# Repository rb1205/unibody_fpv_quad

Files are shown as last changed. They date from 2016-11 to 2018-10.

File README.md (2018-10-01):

# Unibody FPV quad

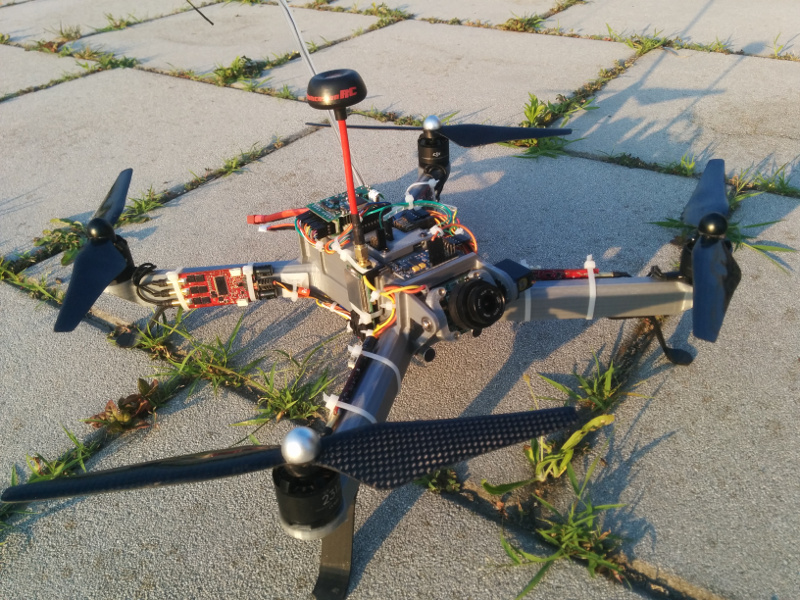
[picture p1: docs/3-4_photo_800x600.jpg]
Quad photo


A size class 400 FPV quadcopter assembled over a single piece FDM printable body, designed for long range freestyle FPV. Some highlights:

* Good FPV flight performances for its class due to high frame rigidity (comparable to frames made from single carbon fiber sheets) and relatively low inertia moment
* servo-operated tiltable FPV CCD camera mount with 180° mechanical range integrated in the unibody frame.
* Frame has dedicated fixing points for video TX, ESC, cables, antenna,...
* Fully documented: [BOM and exploded diagram](https://github.com/rb1205/unibody_fpv_quad/raw/master/docs/assembly.pdf) of the project with all components and screws located, for easy assembly. [Wiring diagram](https://github.com/rb1205/unibody_fpv_quad/raw/master/docs/wiring_diagram.pdf) is provided, too.
* Printable & easly replaceable landing gears

## Stats

* Made for 9" props
* Typical flight time is ~15-20 minutes with a 3300 mAh 4s battery. 
* Weight is 200g for the frame alone, ~700g for the assembled quad without battery and ~1000g with a 3300 mAh 4s lipo battery
* Inertia moments around CoG are around 1, 1 and 2 Kg/dm^2 (pitch,roll,yaw)
* Battery bay size=50x38x120 mm

Due to the frame size, you'll need a bigger-than-average printer with a minimum build envelope of 320x300x50mm to print the body.

CAD files are included in the project, software used is PTC Creo V.2. 

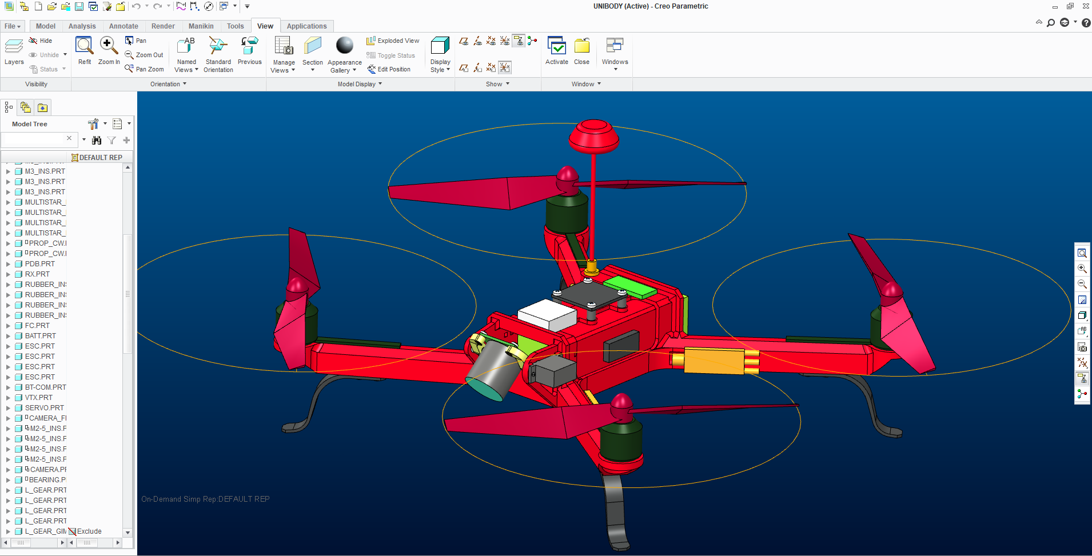
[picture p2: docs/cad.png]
Quad CAD model


Here's a [Video](https://www.youtube.com/watch?v=QMW7MYOoSNg) with a (shitty) test flight.

## Documentation

[Modal analysis](docs/modal_analysis.md)

[Print instructions](docs/print_instructions.md)

[Exploded diagram with BOM](https://github.com/rb1205/unibody_fpv_quad/raw/master/docs/assembly.pdf)

[Wiring diagram](https://github.com/rb1205/unibody_fpv_quad/raw/master/docs/wiring_diagram.pdf)

[Reference flight controller settings for iNav](config_files) (valid only for the powertrain configuration listed in the BOM)

---

This project is released under the terms of [Creative Commons Attribution-NonCommercial license](https://creativecommons.org/licenses/by-nc/4.0/)

Please contact us at riccardo.belloli@inova-soluzioni.it to discuss commercial usage of this project.

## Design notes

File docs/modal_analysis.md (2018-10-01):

# Modal analysis

To estimate the structure's resonating frequencies, an undamped modal analysis has been performed on a quick-and-dirty FEM model of the body with the added mass from the various mounted devices on the relevant places (namely motors+props, battery, top side electronics, PDB, camera subassembly) and a distributed additional body mass to reach the actual total weight. 

The body is supposed to be printed with commercial grade PLA. Material properties have been taken from [here](http://www.makeitfrom.com/material-properties/Polylactic-Acid-PLA-Polylactide/). As the quad arms are a shell filled with light support structure, as a conservative approach the model has the arms completely hollowed on the inside leaving the solid width and height from the reccomanded print settings (3x0.6mm perimeters, 9x0.2 top and bottom layers).

Following figure shows the meshed model

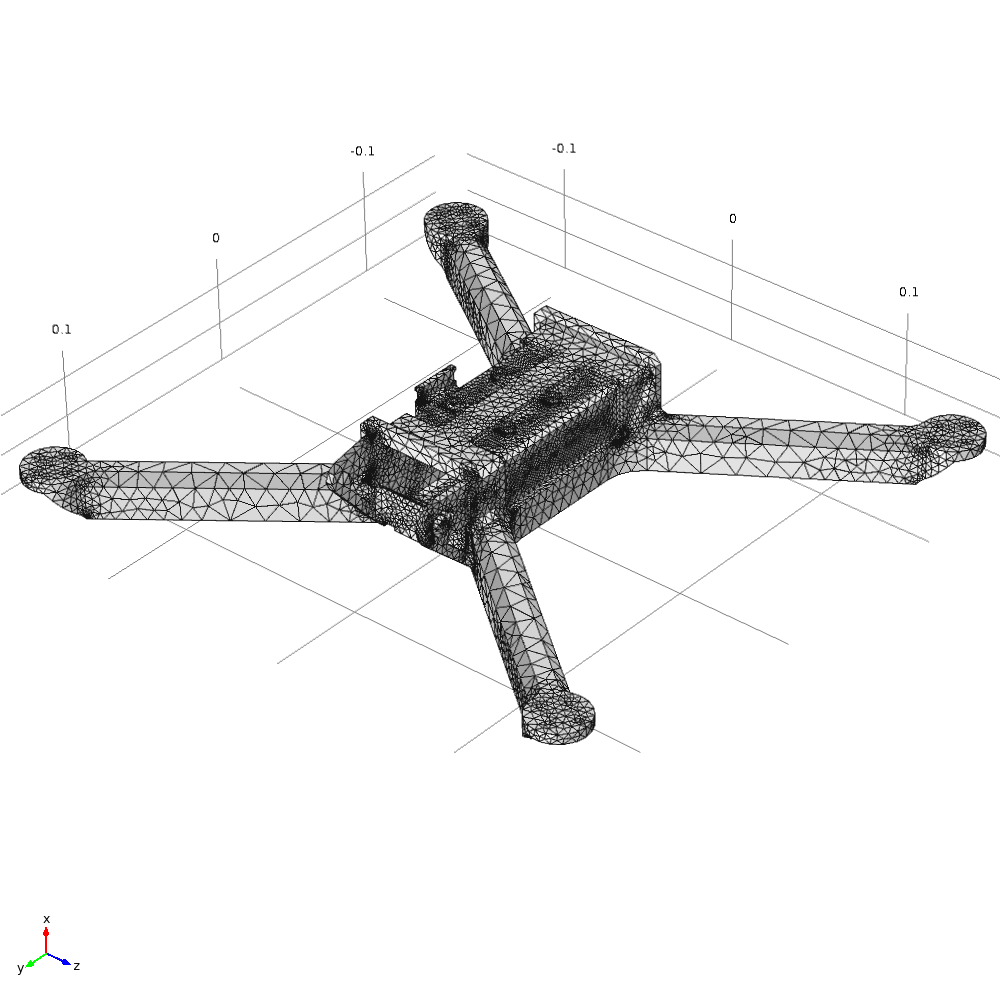
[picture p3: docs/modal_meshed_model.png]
meshed model


Analysis has been performed using Comsol Multiphysics V4.1

## Results

The following figures show the first 3 real eigenfrequencies with the relative modal shapes.

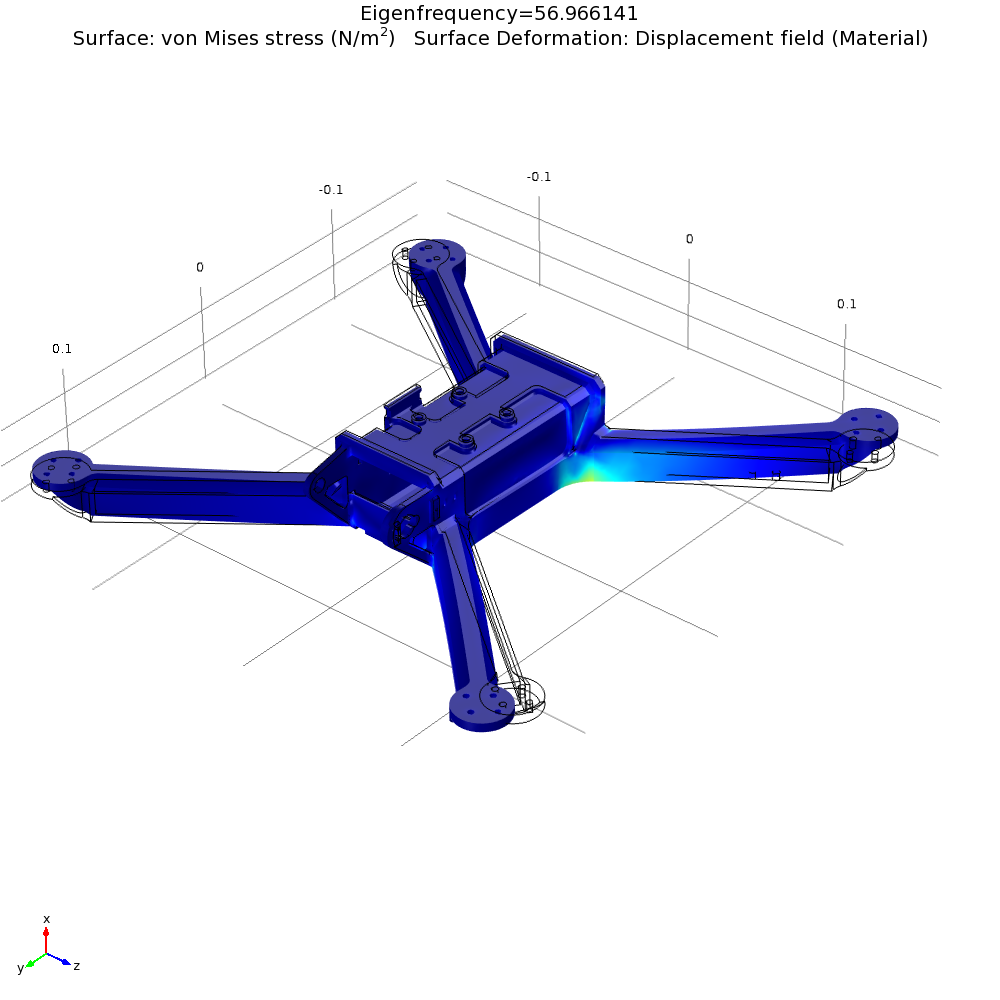
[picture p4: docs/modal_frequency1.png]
1st modal frequency

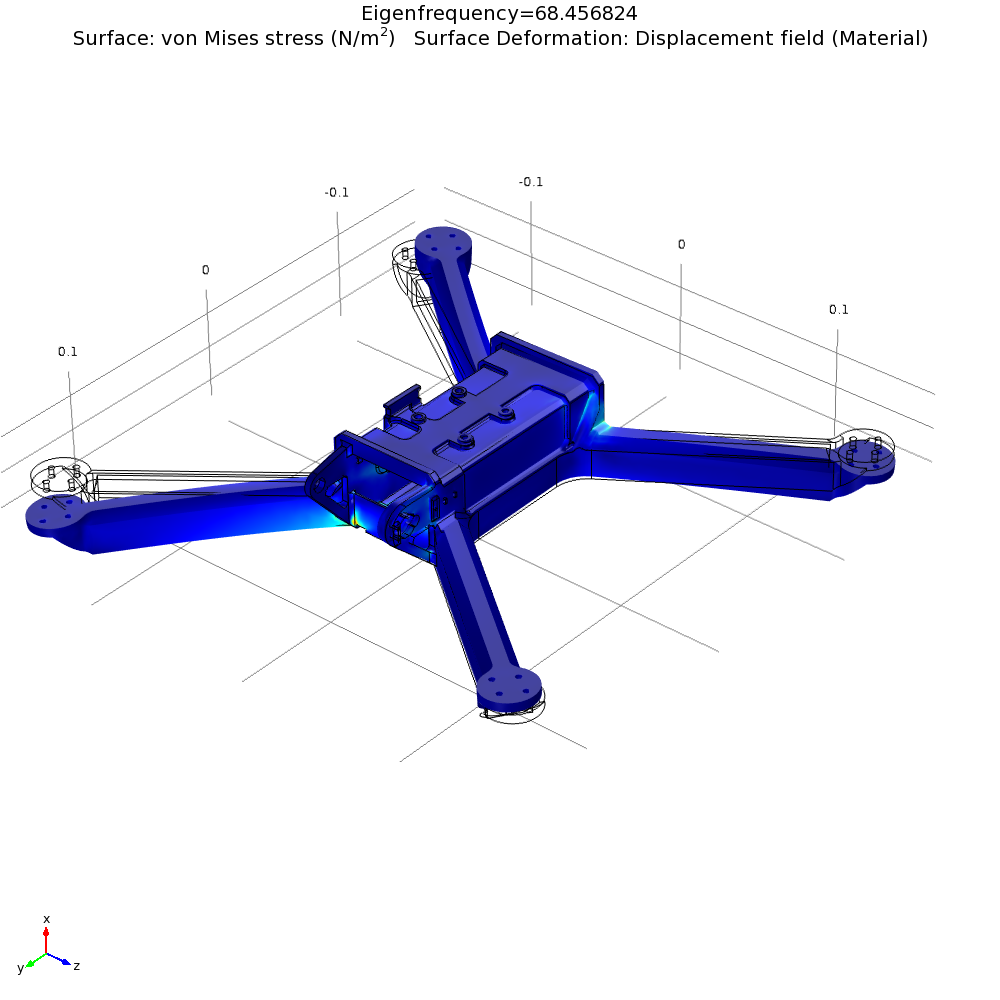
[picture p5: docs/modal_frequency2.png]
2nd modal frequency

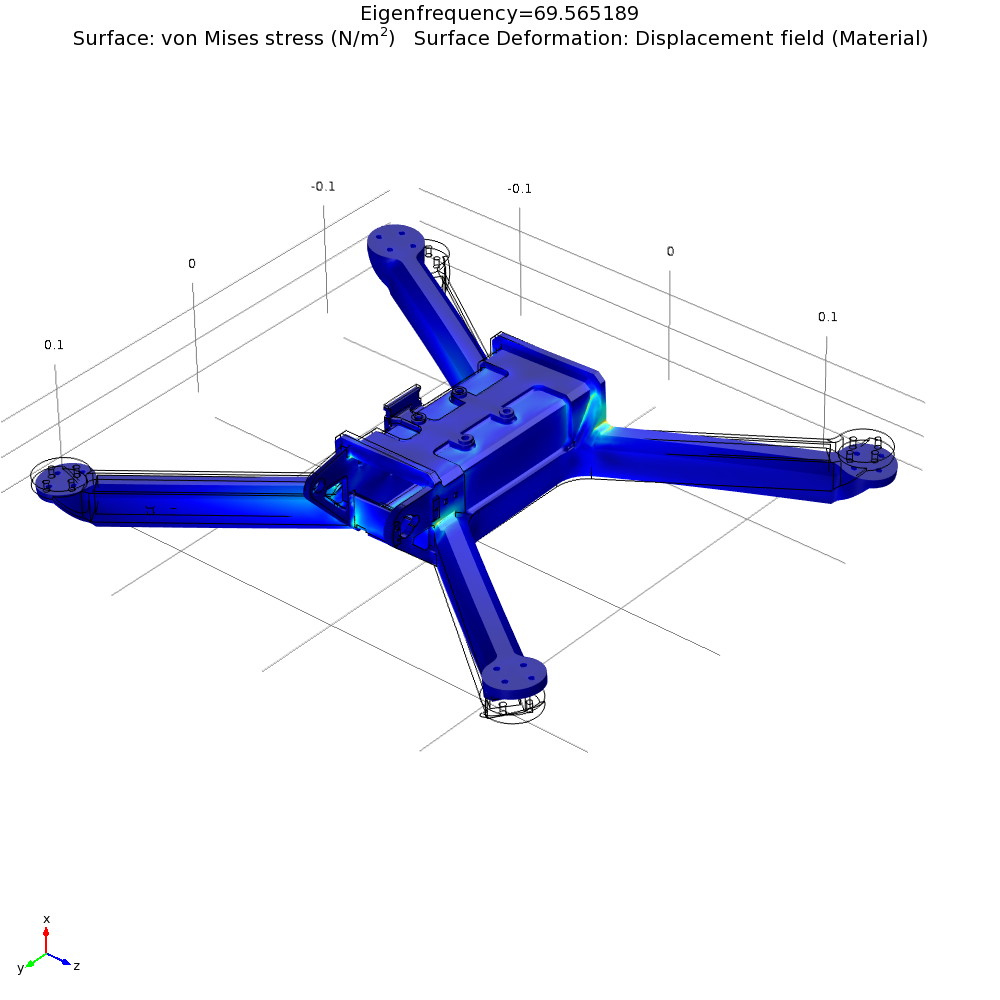
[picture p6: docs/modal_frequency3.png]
3rd modal frequency


The first free body resonation happens at about 56 Hertz and is caused by the arms vibrating on the fixing point on the central box, planarly on the horizontal plane. The second and third frequencies are similar and happen at around 68 hertz, and are due to the arms vibrating out of the horizontal plane.

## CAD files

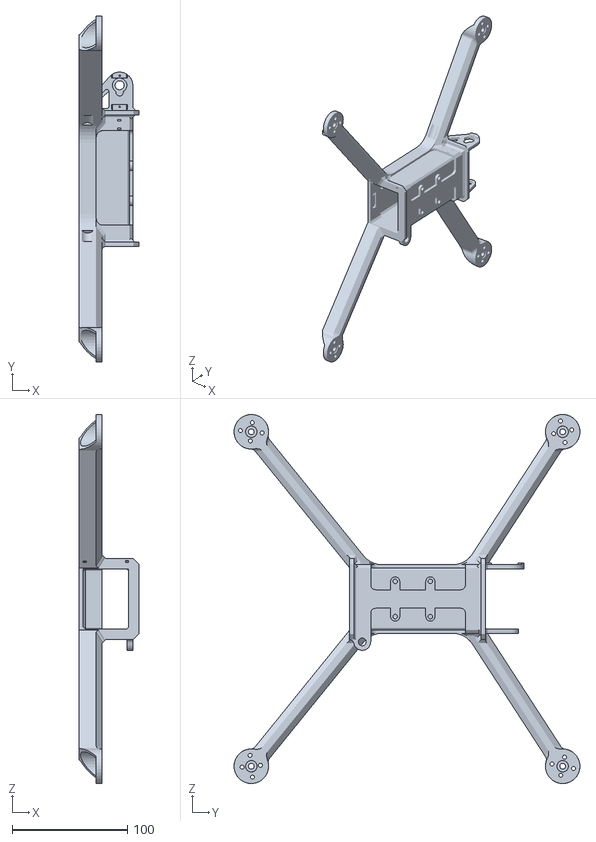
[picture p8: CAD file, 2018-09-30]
stl/body.stl
52.2 x 300.0 x 320.0

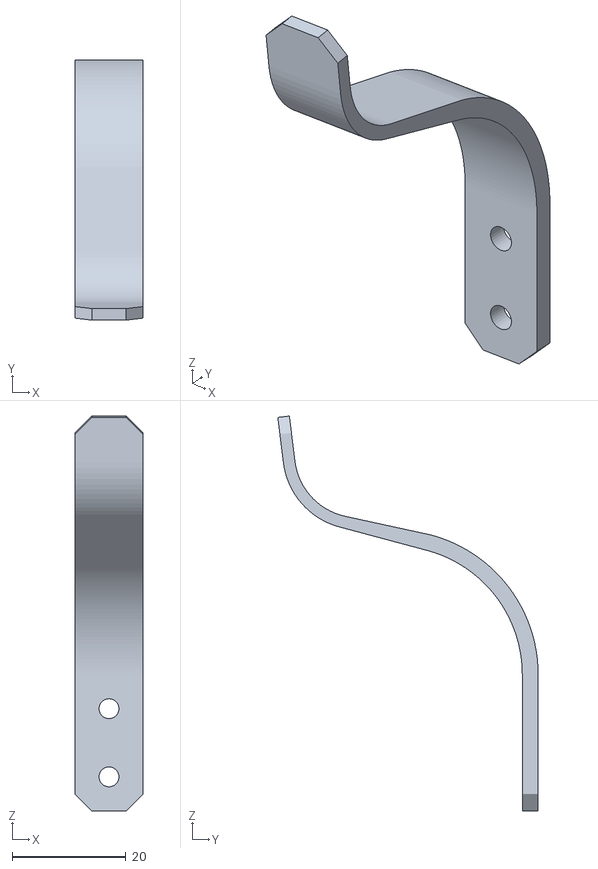
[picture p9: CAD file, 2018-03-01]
stl/l_gear.stl
12.0 x 45.8 x 69.5

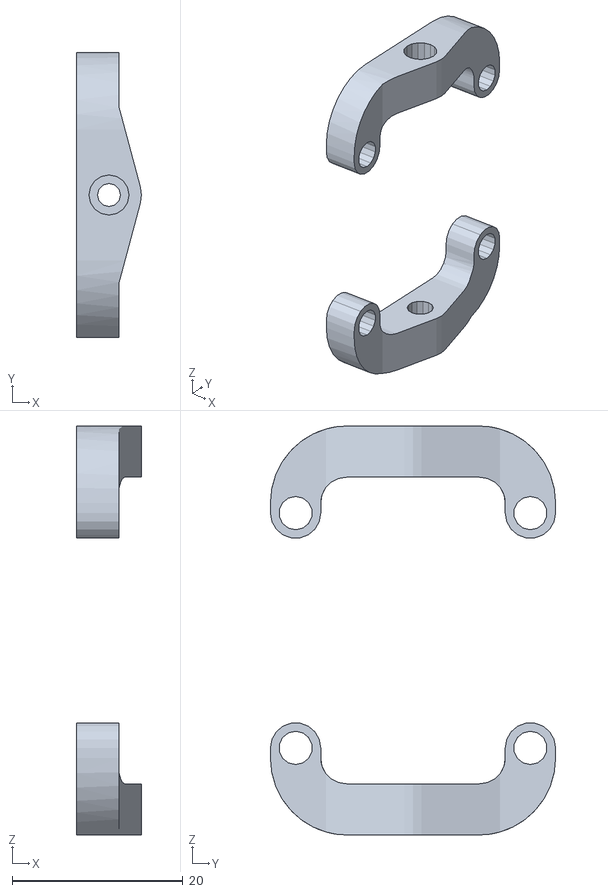
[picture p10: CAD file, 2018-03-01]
stl/camera_frame.stl
7.60 x 33.4 x 47.9

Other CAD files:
docs/wiring_diagram.dwg

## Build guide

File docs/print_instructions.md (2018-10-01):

### Body

To print this part you'll need a printer with a minimum printing envelope of 320x300x50mm.

Please observe the following print parameter carefully. The frame has been designed and verified with these settings, using different parameters may alter basilar charateristics like strength, rigidity, stress concetration points, inertia charateristics....

* Material: PLA 
* Nozzle: 0.5mm
* Extrusion width: 0.6mm
* Perimeter outlines: 3
* Layer height: 10mm
* Top solid layers: 9
* Bottom solid layers: 9
* Infill pattern: honeycomb

You are free to set all the remaining printing options as they best suit your printer.

##### Support

You'll need support structures to print the motor support pads, the cutouts near the camera mount and the top of the battery box, and expecially the latter may become hard to remove. To make it simple, set your slicer to build the support parallel to the lateral walls, so that you can extract it by pulling from the open end. The following figure shows what the preview should look like (slicer: simplify3d).
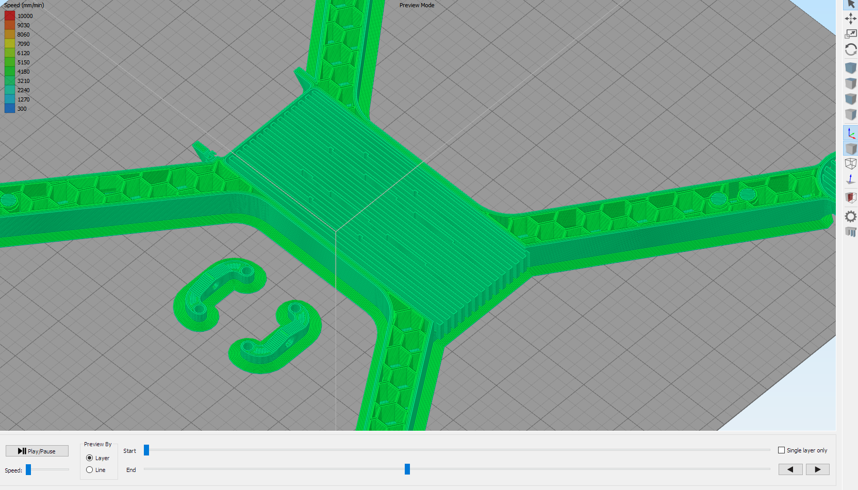
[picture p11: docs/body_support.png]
Support material example


Make sure the slicer is not placing any support in the antenna passage!

### Landing gears

Material: Carbon fiber loaded nylon or ABS

Print this part completely solid

### Camera Frame

Material: Whatever

You're free to print this part as you wish as long as the resulting part is completely solid.

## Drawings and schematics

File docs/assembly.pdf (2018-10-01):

1

A

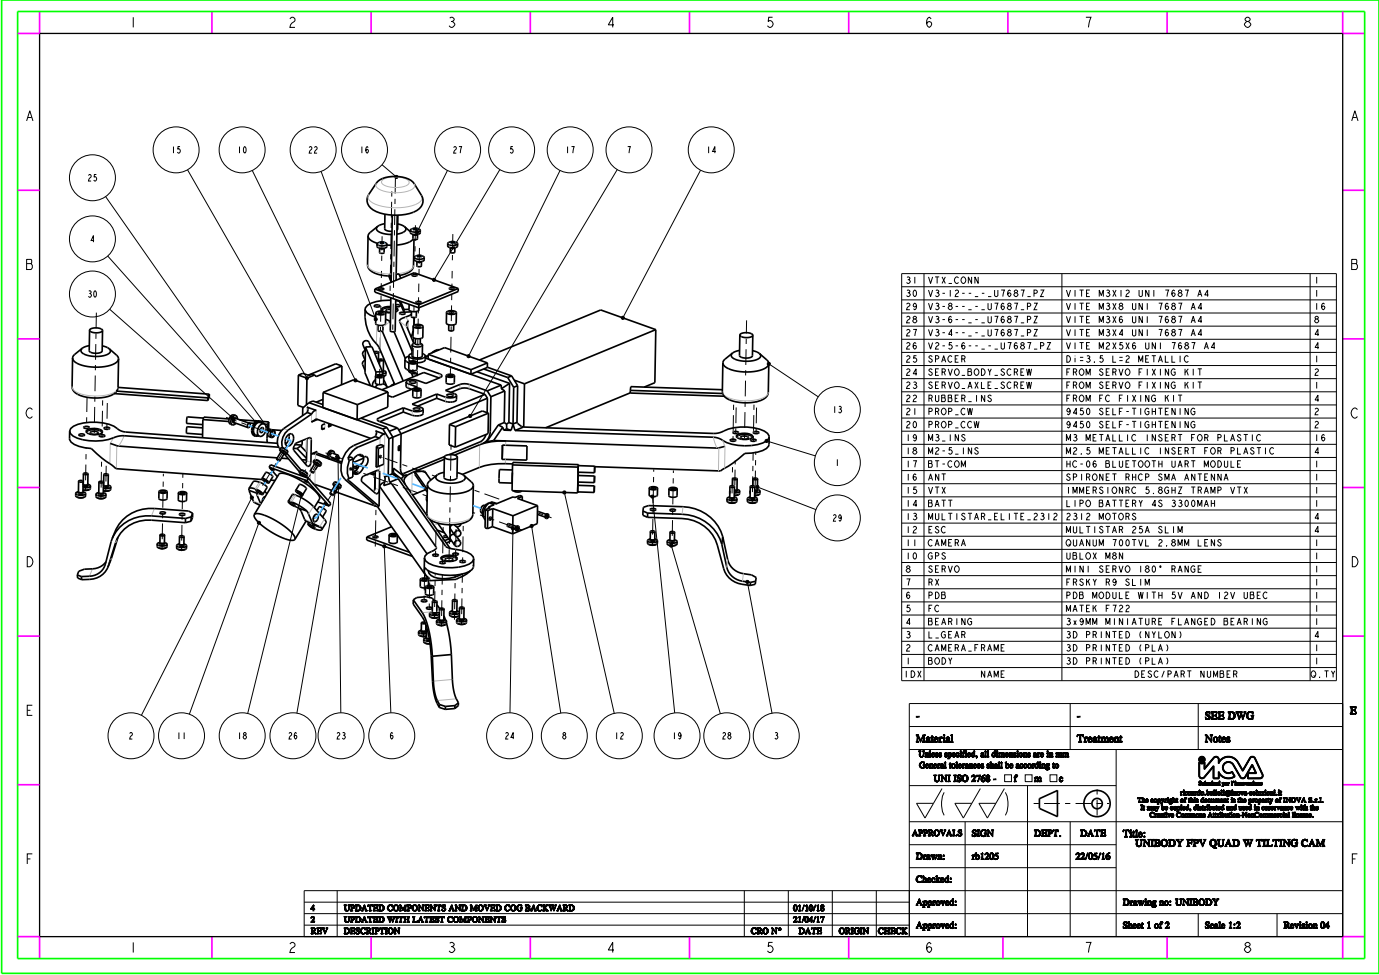
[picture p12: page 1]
SEE DWG; Material; Treatment; Notes; APPROVALS SIGN; DEPT.; DATE; Drawn:; Checked:; Approved:; Drawing no: UNIBODY; Sheet 1 of 2; Scale 1:2; Revision 04; UPDATED COMPONENTS AND MOVED COG BACKWARD; UPDATED WITH LATEST COMPONENTS; REV; DESCRIPTION; CRO N°; ORIGIN CHECK; IDX; NAME; DESC/PART NUMBER; 1 BODY; 3D PRINTED (PLA); 2 CAMERA_FRAME; 3 L_GEAR; 3D PRINTED (NYLON); 4 BEARING; 3x9MM MINIATURE FLANGED BEARING; MATEK F722; 6 PDB; PDB MODULE WITH 5V AND 12V UBEC; FRSKY R9 SLIM; 8 SERVO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

Unless specified, all dimensions are in mm
General tolerances shall be according to
UNI ISO 2768 - o-

Soluzioni per l'innovazione
riccardo.belloli@inova-soluzioni.it

The copyright of this document is the property of INOVA S.r.l.
It may be copied, distributed and used in osservance with the
Creative Commons Attribution-NonCommercial license.
Title:
UNIBODY FPV QUAD W TILTING CAM

1

A

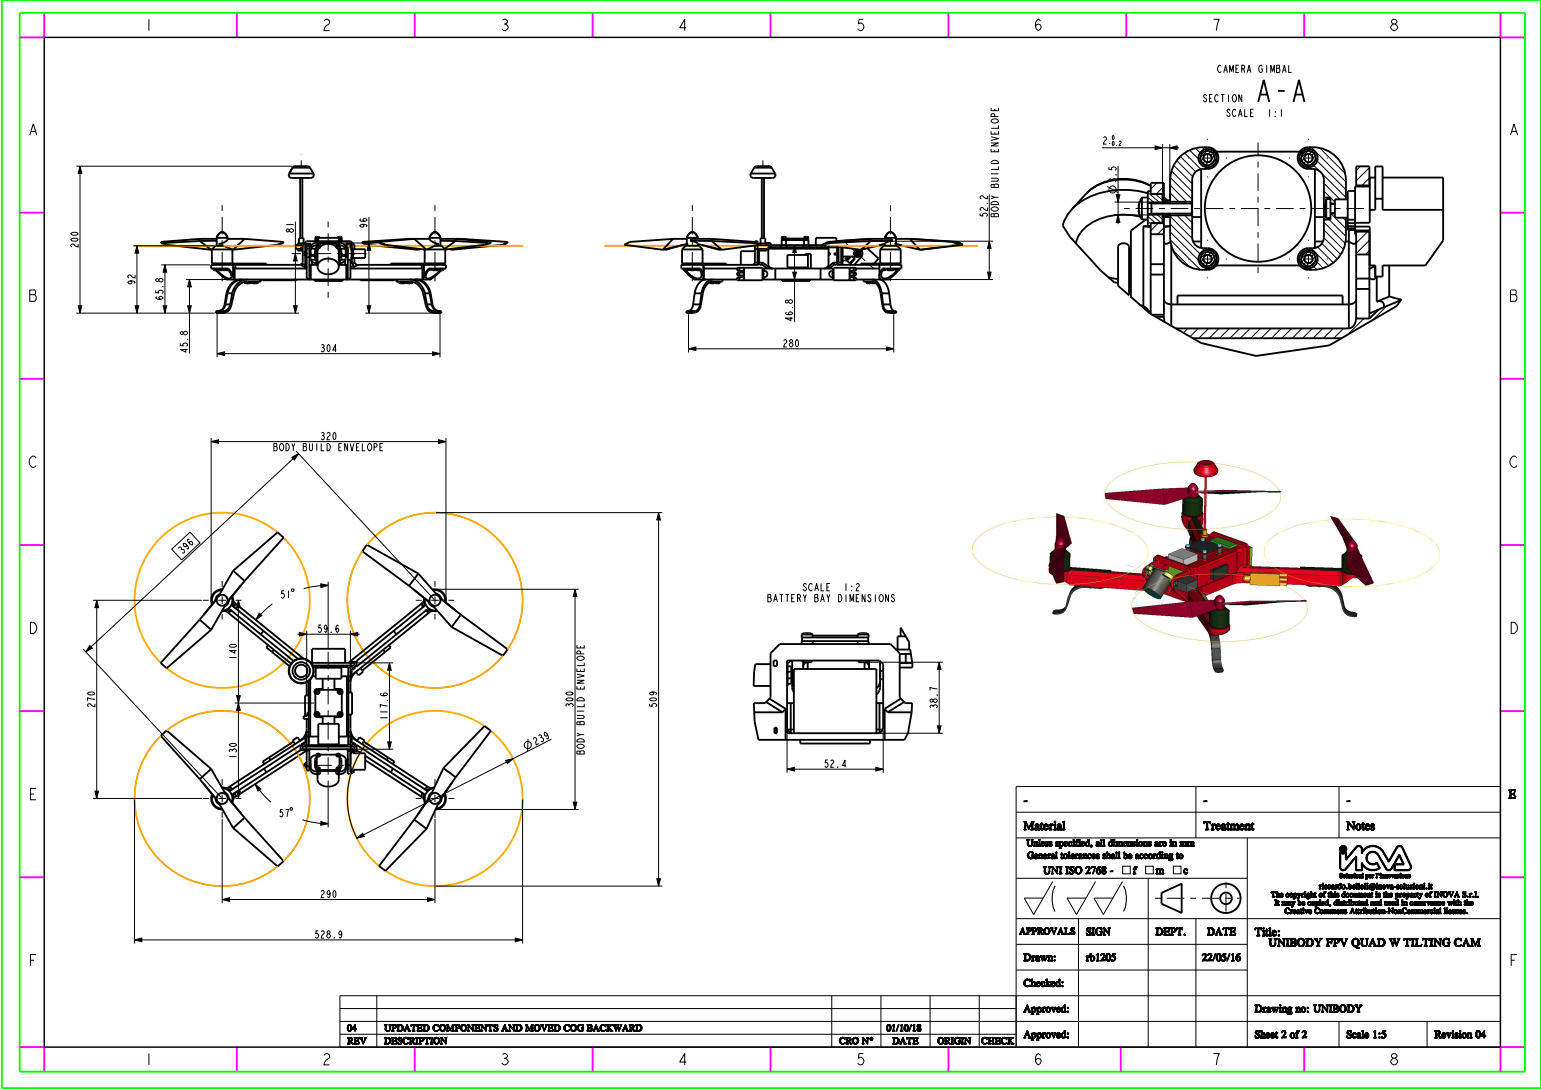
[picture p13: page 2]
Material; Treatment; Notes; APPROVALS SIGN; DEPT.; DATE; Drawn:; Checked:; Approved:; Drawing no: UNIBODY; Sheet 2 of 2; Scale 1:5; Revision 04 ⁰⁴; UPDATED COMPONENTS AND MOVED COG BACKWARD; REV; DESCRIPTION; CRO N°; ORIGIN CHECK; CAMERA GIMBAL SECTION A-A SCALE 1:1

BODY BUILD ENVELOPE

SCALE 1:2
BATTERY BAY DIMENSIONS

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

Soluzioni per l'innovazione
riccardo.belloli@inova-soluzioni.it

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

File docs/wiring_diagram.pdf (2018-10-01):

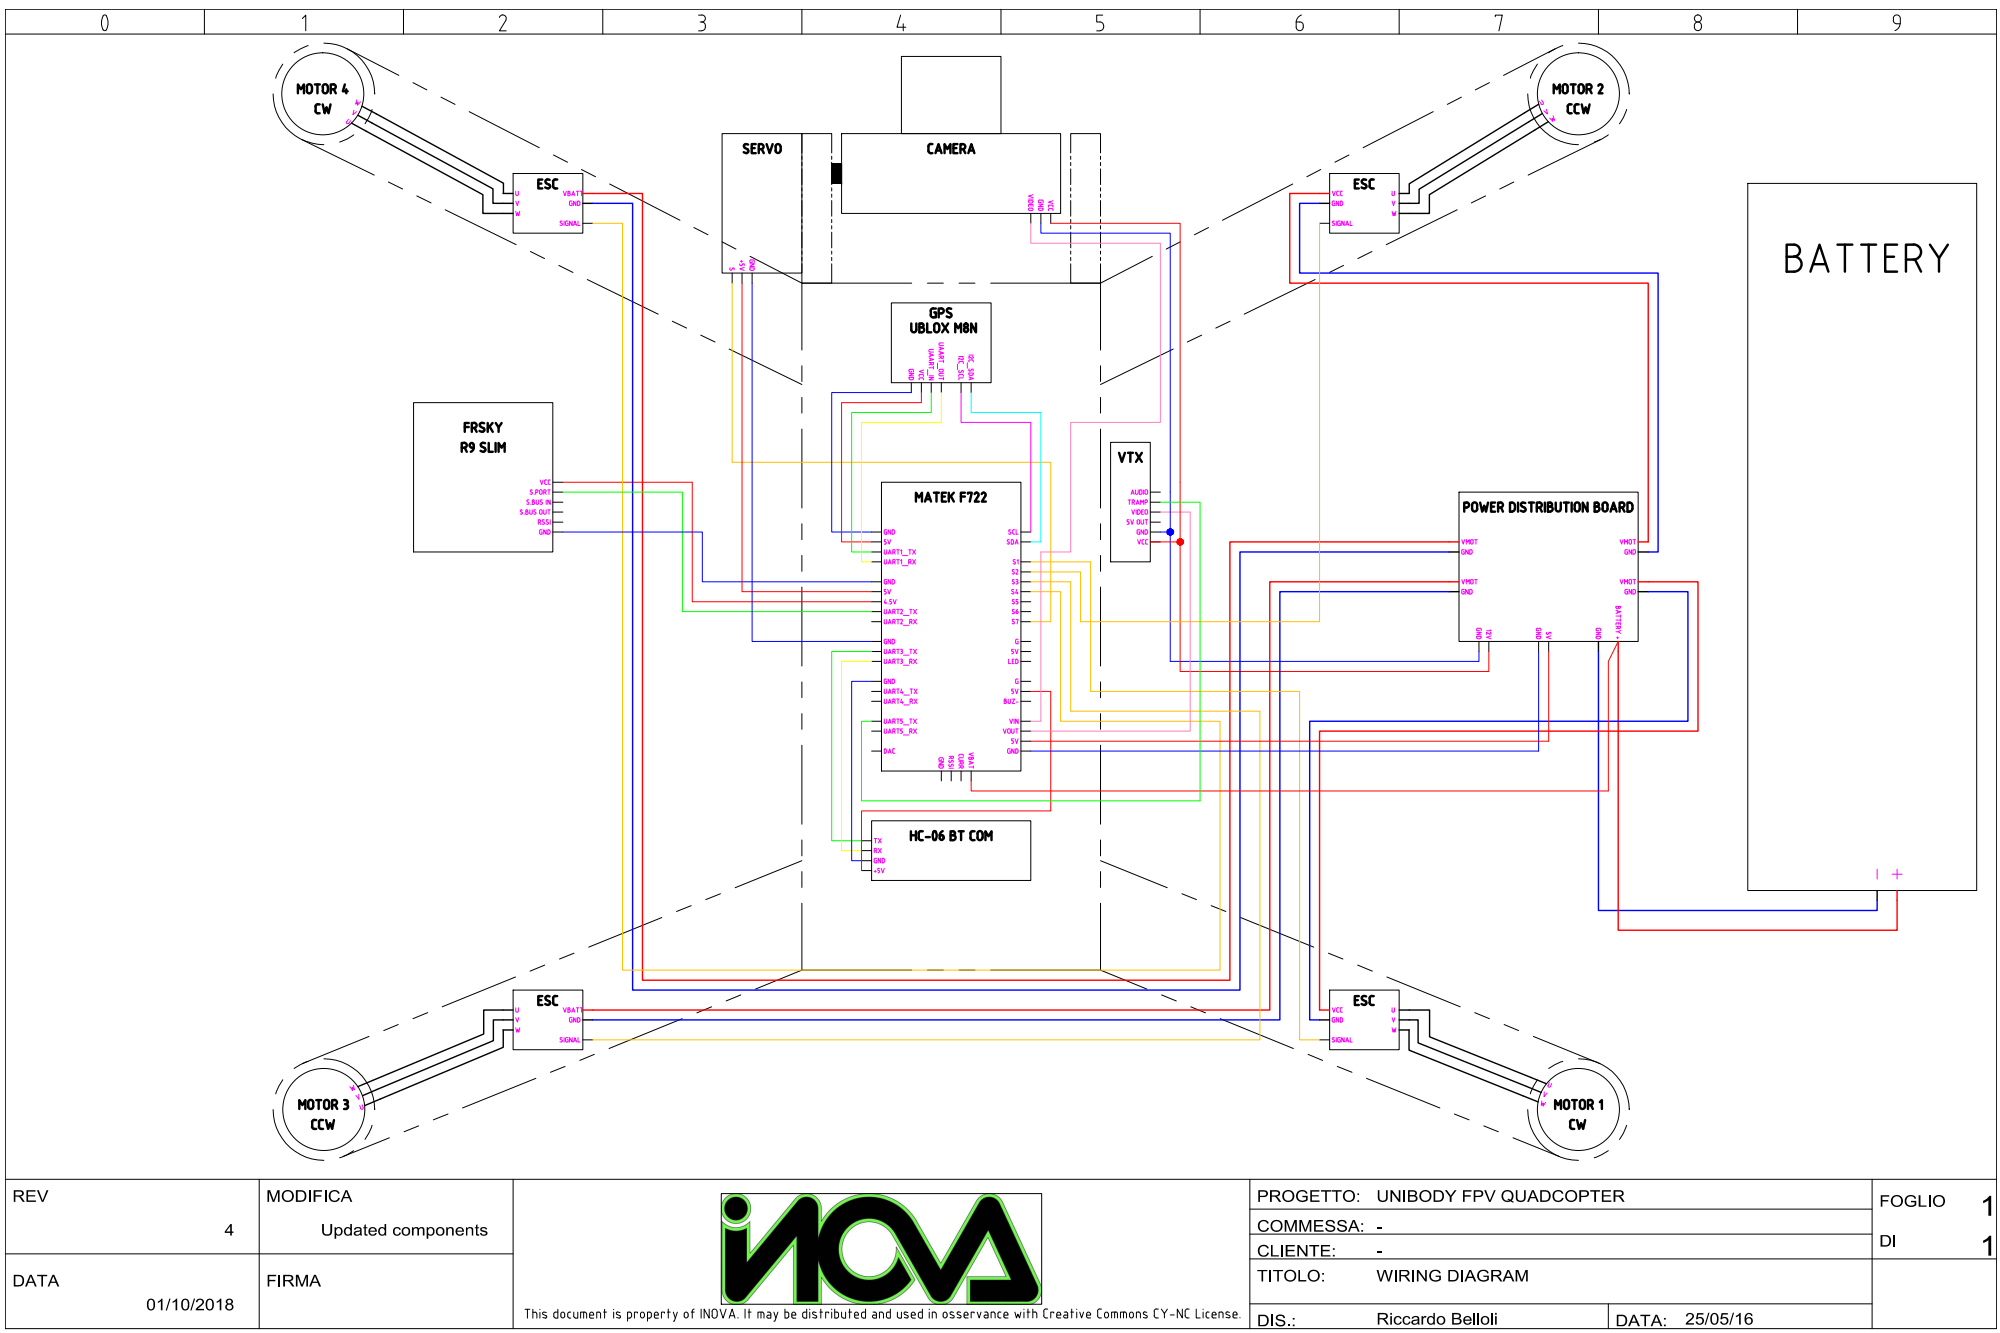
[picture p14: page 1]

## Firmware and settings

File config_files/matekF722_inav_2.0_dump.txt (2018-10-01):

# version
# INAV/MATEKF722 2.0.0 Aug 20 2018 / 19:21:31 (dbdd1656a)

# resources

# mixer

mmix reset

mmix 0  1.000 -1.000  1.000 -1.000
mmix 1  1.000 -1.000 -1.000  1.000
mmix 2  1.000  1.000  1.000  1.000
mmix 3  1.000  1.000 -1.000 -1.000

# servo mix
smix reset

smix 0 1 12 100 0
smix 1 1 9 100 0
smix 2 0 12 100 0

# servo
servo 0 1000 2000 1500 100
servo 1 700 2300 1500 100
servo 2 1000 2000 1500 100
servo 3 1000 2000 1500 100
servo 4 1000 2000 1500 100
servo 5 1000 2000 1500 100
servo 6 1000 2000 1500 100
servo 7 1000 2000 1500 100

# feature
feature -THR_VBAT_COMP
feature -VBAT
feature -TX_PROF_SEL
feature -BAT_PROF_AUTOSWITCH
feature -MOTOR_STOP
feature -SOFTSERIAL
feature -GPS
feature -TELEMETRY
feature -CURRENT_METER
feature -3D
feature -RX_PARALLEL_PWM
feature -RX_MSP
feature -RSSI_ADC
feature -LED_STRIP
feature -DASHBOARD
feature -BLACKBOX
feature -TRANSPONDER
feature -AIRMODE
feature -SUPEREXPO
feature -VTX
feature -RX_SPI
feature -PWM_SERVO_DRIVER
feature -PWM_OUTPUT_ENABLE
feature -OSD
feature -FW_LAUNCH
feature -TRACE
feature VBAT
feature TELEMETRY
feature CURRENT_METER
feature LED_STRIP
feature BLACKBOX
feature PWM_OUTPUT_ENABLE
feature OSD

# beeper
beeper RUNTIME_CALIBRATION
beeper HW_FAILURE
beeper RX_LOST
beeper RX_LOST_LANDING
beeper DISARMING
beeper ARMING
beeper ARMING_GPS_FIX
beeper BAT_CRIT_LOW
beeper BAT_LOW
beeper GPS_STATUS
beeper RX_SET
beeper ACTION_SUCCESS
beeper ACTION_FAIL
beeper READY_BEEP
beeper MULTI_BEEPS
beeper DISARM_REPEAT
beeper ARMED
beeper SYSTEM_INIT
beeper ON_USB
beeper LAUNCH_MODE
beeper CAM_CONNECTION_OPEN
beeper CAM_CONNECTION_CLOSED

# map
map AETR

# serial
serial 20 1 115200 38400 0 115200
serial 0 0 115200 38400 0 115200
serial 1 64 115200 38400 0 115200
serial 2 2 115200 38400 0 115200
serial 3 0 115200 38400 0 115200
serial 4 4096 115200 38400 0 115200

# led
led 0 0,0::AOW:10
led 1 1,0::AOW:1
led 2 2,0::AOW:1
led 3 3,0::AOW:1
led 4 4,0::AOW:1
led 5 5,0::AOW:10
led 6 0,0::C:0
led 7 0,0::C:0
led 8 0,0::C:0
led 9 0,0::C:0
led 10 0,0::C:0
led 11 0,0::C:0
led 12 0,0::C:0
led 13 0,0::C:0
led 14 0,0::C:0
led 15 0,0::C:0
led 16 0,0::C:0
led 17 0,0::C:0
led 18 0,0::C:0
led 19 0,0::C:0
led 20 0,0::C:0
led 21 0,0::C:0
led 22 0,0::C:0
led 23 0,0::C:0
led 24 0,0::C:0
led 25 0,0::C:0
led 26 0,0::C:0
led 27 0,0::C:0
led 28 0,0::C:0
led 29 0,0::C:0
led 30 0,0::C:0
led 31 0,0::C:0

# color
color 0 0,0,0
color 1 0,255,255
color 2 0,0,255
color 3 30,0,255
color 4 60,0,255
color 5 90,0,255
color 6 120,0,255
color 7 150,0,255
color 8 180,0,255
color 9 210,0,255
color 10 240,0,255
color 11 270,0,255
color 12 300,0,255
color 13 330,0,255
color 14 0,0,0
color 15 0,0,0

# mode_color
mode_color 0 0 1
mode_color 0 1 11
mode_color 0 2 2
mode_color 0 3 13
mode_color 0 4 10
mode_color 0 5 3
mode_color 1 0 5
mode_color 1 1 11
mode_color 1 2 3
mode_color 1 3 13
mode_color 1 4 10
mode_color 1 5 3
mode_color 2 0 10
mode_color 2 1 11
mode_color 2 2 4
mode_color 2 3 13
mode_color 2 4 10
mode_color 2 5 3
mode_color 3 0 8
mode_color 3 1 11
mode_color 3 2 4
mode_color 3 3 13
mode_color 3 4 10
mode_color 3 5 3
mode_color 4 0 7
mode_color 4 1 11
mode_color 4 2 3
mode_color 4 3 13
mode_color 4 4 10
mode_color 4 5 3
mode_color 5 0 9
mode_color 5 1 11
mode_color 5 2 2
mode_color 5 3 13
mode_color 5 4 10
mode_color 5 5 3
mode_color 6 0 2
mode_color 6 1 6
mode_color 6 2 1
mode_color 6 3 0
mode_color 6 4 0
mode_color 6 5 2
mode_color 6 6 3
mode_color 6 7 6
mode_color 6 8 0
mode_color 6 9 0
mode_color 6 10 0

# aux
aux 0 0 0 1350 2100
aux 1 1 2 1800 2100
aux 2 2 2 1350 1650
aux 3 20 0 1800 2100
aux 4 4 5 1350 1650
aux 5 5 5 1800 2100
aux 6 6 8 900 1200
aux 7 7 10 1400 1600
aux 8 3 4 1350 2100
aux 9 9 3 1050 2100
aux 10 8 3 1800 2100
aux 11 19 3 1350 1650
aux 12 21 8 1800 2100
aux 13 11 10 1800 2100
aux 14 15 6 1800 2100
aux 15 18 7 1800 2100
aux 16 32 6 1800 2100
aux 17 0 0 900 900
aux 18 0 0 900 900
aux 19 0 0 900 900

# adjrange
adjrange 0 0 0 900 900 0 0
adjrange 1 0 0 900 900 0 0
adjrange 2 0 0 900 900 0 0
adjrange 3 0 0 900 900 0 0
adjrange 4 0 0 900 900 0 0
adjrange 5 0 0 900 900 0 0
adjrange 6 0 0 900 900 0 0
adjrange 7 0 0 900 900 0 0
adjrange 8 0 0 900 900 0 0
adjrange 9 0 0 900 900 0 0
adjrange 10 0 0 900 900 0 0
adjrange 11 0 0 900 900 0 0

# rxrange
rxrange 0 1000 2000
rxrange 1 1000 2000
rxrange 2 1000 2000
rxrange 3 1000 2000

# osd_layout
osd_layout 0 0 25 12 V
osd_layout 0 1 12 0 H
osd_layout 0 2 0 0 H
osd_layout 0 3 8 6 V
osd_layout 0 4 8 6 V
osd_layout 0 5 23 8 H
osd_layout 0 6 23 9 H
osd_layout 0 7 12 13 V
osd_layout 0 8 20 2 H
osd_layout 0 9 1 2 H
osd_layout 0 10 1 1 H
osd_layout 0 11 1 13 V
osd_layout 0 12 1 12 V
osd_layout 0 13 1 7 V
osd_layout 0 14 25 13 V
osd_layout 0 15 24 7 V
osd_layout 0 16 2 10 H
osd_layout 0 17 2 11 H
osd_layout 0 18 2 12 H
osd_layout 0 19 15 1 H
osd_layout 0 20 18 12 H
osd_layout 0 21 0 12 H
osd_layout 0 22 14 3 V
osd_layout 0 23 2 1 V
osd_layout 0 24 12 2 H
osd_layout 0 25 22 5 H
osd_layout 0 26 24 7 H
osd_layout 0 27 3 5 H
osd_layout 0 28 22 1 V
osd_layout 0 29 23 12 H
osd_layout 0 30 1 14 V
osd_layout 0 31 0 10 H
osd_layout 0 32 12 0 V
osd_layout 0 33 6 2 H
osd_layout 0 34 10 2 V
osd_layout 0 35 1 5 H
osd_layout 0 36 1 5 H
osd_layout 0 37 1 6 H
osd_layout 0 38 24 2 H
osd_layout 0 39 1 5 H
osd_layout 0 40 1 2 H
osd_layout 0 41 1 8 H
osd_layout 0 42 1 7 H
osd_layout 0 43 0 0 H
osd_layout 0 44 0 0 H
osd_layout 0 45 0 0 H
osd_layout 0 46 3 6 H
osd_layout 0 47 3 7 H
osd_layout 0 48 23 7 H
osd_layout 0 49 23 6 H
osd_layout 0 50 0 0 H
osd_layout 0 51 12 2 H
osd_layout 0 52 12 2 H
osd_layout 0 53 12 1 H
osd_layout 0 54 12 1 V
osd_layout 0 55 18 0 V
osd_layout 0 56 2 12 H
osd_layout 0 57 2 12 H
osd_layout 0 58 2 12 H
osd_layout 0 59 2 12 H
osd_layout 0 60 2 12 H
osd_layout 0 61 2 12 H
osd_layout 0 62 2 10 H
osd_layout 0 63 2 11 H
osd_layout 0 64 2 12 H
osd_layout 0 65 2 12 H
osd_layout 0 66 2 12 H
osd_layout 0 67 2 12 H
osd_layout 0 68 2 12 H
osd_layout 0 69 2 12 H
osd_layout 0 70 2 12 H
osd_layout 0 71 2 12 H
osd_layout 0 72 2 12 H
osd_layout 0 73 2 12 H
osd_layout 0 74 2 12 H
osd_layout 0 75 2 12 H
osd_layout 0 76 2 12 H
osd_layout 0 77 2 12 H
osd_layout 0 78 0 0 H
osd_layout 0 79 2 12 H
osd_layout 0 80 2 12 H
osd_layout 0 81 2 12 H
osd_layout 0 82 2 12 H
osd_layout 0 83 2 12 H
osd_layout 0 84 2 12 H
osd_layout 1 0 23 0 V
osd_layout 1 1 12 0 H
osd_layout 1 2 0 0 H
osd_layout 1 3 8 6 H
osd_layout 1 4 8 6 H
osd_layout 1 5 23 8 H
osd_layout 1 6 23 9 H
osd_layout 1 7 12 12 H
osd_layout 1 8 20 2 H
osd_layout 1 9 1 2 H
osd_layout 1 10 1 1 V
osd_layout 1 11 1 3 H
osd_layout 1 12 1 4 H
osd_layout 1 13 23 1 H
osd_layout 1 14 25 13 V
osd_layout 1 15 1 0 H
osd_layout 1 16 2 10 H
osd_layout 1 17 2 11 H
osd_layout 1 18 2 12 H
osd_layout 1 19 15 1 H
osd_layout 1 20 9 14 V
osd_layout 1 21 9 13 V
osd_layout 1 22 14 11 H
osd_layout 1 23 1 13 V
osd_layout 1 24 12 2 H
osd_layout 1 25 23 5 H
osd_layout 1 26 24 7 H
osd_layout 1 27 3 5 H
osd_layout 1 28 23 11 H
osd_layout 1 29 23 14 V
osd_layout 1 30 1 13 H
osd_layout 1 31 25 12 V
osd_layout 1 32 12 1 H
osd_layout 1 33 6 2 H
osd_layout 1 34 18 2 H
osd_layout 1 35 1 5 H
osd_layout 1 36 1 5 H
osd_layout 1 37 1 6 H
osd_layout 1 38 1 7 H
osd_layout 1 39 1 5 H
osd_layout 1 40 1 2 H
osd_layout 1 41 1 8 H
osd_layout 1 42 1 7 H
osd_layout 1 43 0 0 V
osd_layout 1 44 0 0 H
osd_layout 1 45 0 0 H
osd_layout 1 46 1 12 H
osd_layout 1 47 1 12 H
osd_layout 1 48 23 7 H
osd_layout 1 49 23 6 H
osd_layout 1 50 0 0 H
osd_layout 1 51 1 12 H
osd_layout 1 52 1 13 H
osd_layout 1 53 12 1 H
osd_layout 1 54 12 1 H
osd_layout 1 55 1 8 H
osd_layout 1 56 2 12 H
osd_layout 1 57 2 12 H
osd_layout 1 58 2 12 H
osd_layout 1 59 2 12 H
osd_layout 1 60 2 12 H
osd_layout 1 61 2 12 H
osd_layout 1 62 2 10 H
osd_layout 1 63 2 11 H
osd_layout 1 64 2 12 H
osd_layout 1 65 2 12 H
osd_layout 1 66 2 12 H
osd_layout 1 67 2 12 H
osd_layout 1 68 2 12 H
osd_layout 1 69 2 12 H
osd_layout 1 70 2 12 H
osd_layout 1 71 2 12 H
osd_layout 1 72 2 12 H
osd_layout 1 73 2 12 H
osd_layout 1 74 2 12 H
osd_layout 1 75 2 12 H
osd_layout 1 76 2 12 H
osd_layout 1 77 2 12 H
osd_layout 1 78 0 0 H
osd_layout 1 79 2 12 H
osd_layout 1 80 2 12 H
osd_layout 1 81 2 12 H
osd_layout 1 82 2 12 H
osd_layout 1 83 2 12 H
osd_layout 1 84 2 12 H
osd_layout 2 0 23 0 H
osd_layout 2 1 12 0 H
osd_layout 2 2 0 0 H
osd_layout 2 3 8 6 H
osd_layout 2 4 8 6 H
osd_layout 2 5 23 8 H
osd_layout 2 6 23 9 H
osd_layout 2 7 12 12 H
osd_layout 2 8 20 2 H
osd_layout 2 9 1 2 H
osd_layout 2 10 8 6 H
osd_layout 2 11 1 3 H
osd_layout 2 12 1 4 H
osd_layout 2 13 23 1 H
osd_layout 2 14 0 11 H
osd_layout 2 15 1 0 H
osd_layout 2 16 2 10 H
osd_layout 2 17 2 11 H
osd_layout 2 18 2 12 H
osd_layout 2 19 15 1 H
osd_layout 2 20 18 12 H
osd_layout 2 21 0 12 H
osd_layout 2 22 14 11 H
osd_layout 2 23 1 1 H
osd_layout 2 24 12 2 H
osd_layout 2 25 23 5 H
osd_layout 2 26 24 7 H
osd_layout 2 27 3 5 H
osd_layout 2 28 23 11 H
osd_layout 2 29 23 12 H
osd_layout 2 30 1 13 H
osd_layout 2 31 0 10 H
osd_layout 2 32 12 1 H
osd_layout 2 33 6 2 H
osd_layout 2 34 18 2 H
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

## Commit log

2016-11-07 First version (no FPV)
    [body.stl, piedino.stl]
2016-11-07 Second version
    [body.stl, carrello.stl, naze32acro_top_telemetry.stl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]
2016-11-07 Cleanup for mk3
    [body.stl, carrello.stl, naze32acro_top_telemetry.stl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]
2016-11-07 added note about threaded inserts
2016-11-07 moved stl's from cad to dedicated directory
    [body.stl, camera_frame.stl, l_gear.stl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]
2016-11-07 added wiring diagram
    [wiring_diagram.dwg]
2016-11-07 added photos and cad window
2016-11-07 Printing instructions added
2016-11-07 updated cad model indexes
2016-11-07 Exported STEP of printable models
    [body.stp, camera_frame.stp, l_gear.stp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]
2016-11-07 STL updated, cover updated for new FC
    [body.stl, l_gear.stl, naze32cover.stl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]
2016-11-07 step dir removed
    [body.stp, camera_frame.stp, l_gear.stp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]
2016-11-17 Reduced arm height by 2mm, added hole for antenna, minor changes
    [body.stl, l_gear.stl]
2016-11-21 FC and OSD configuration files added
    [inav_dump.txt]
2016-11-22 Renamed setting dump file
    [inav_dump.txt, spf3evo_inav_1.3_dump.txt]
2016-12-31 updated config to iNav 1.4
    [spf3evo_inav_1.4_dump.txt]
2017-01-31 Updated config to iNav 1.5.1
    [sp3evo_inav_1.5.1_dump.txt, spf3evo_inav_1.4_dump.txt]
2017-01-31 Changed motor to multistar elite 2312, fixed few dimensions and chamfers
2017-02-07 Reduced motor pad size
2017-02-14 Added attach points, interface and elonged skids for camera gimbal
2017-03-13 changed servo, switched to 2 screws instead of 3
2017-03-14 Wiring diagram updated
    [wiring_diagram.dwg]
2017-04-21 Reduced arms width by 2mm
    [body.stl]
2017-04-21 Minor changes to models
    [camera_frame.stl]
2017-04-21 Documentation update
    [wiring_diagram.dwg]
2017-04-21 Added configuration for inav 1.6.1
    [sp3evo_inav_1.5.1_dump.txt, sp3evo_inav_1.6.1_dump.txt]
2017-04-27 Added V and cap batt monitoring, improved PIDs
    [sp3evo_inav_1.6.1_dump.txt]
2017-04-28 Center of thrust moved 6mm in front of CoG, to compensate for ~10% more thrust that the rear motors are providing.
2017-05-02 Added threaded inserts, updated drawing
2017-05-02 Configuration tweaks
    [sp3evo_inav_1.6.1_dump.txt]
2017-05-02 added default configuration for build
    [sp3evo_inav_1.6.1_defaults.txt]
2017-05-06 Changed LEDs and min cell voltage
    [sp3evo_inav_1.6.1_dump.txt]
2017-05-06 Added configuration for inav 1.7
    [sp3evo_inav_1.7_defaults.txt, sp3evo_inav_1.7_dump.txt]
2017-05-09 Deprecated config for inav 1.5.1
    [sp3evo_inav_1.5.1_dump.txt]
2017-05-09 Aligned IMU, tweaked vbat_scale
    [sp3evo_inav_1.7_dump.txt]
2017-06-08 Added configuration for inav 1.7.1
    [sp3evo_inav_1.7.1_defaults.txt, sp3evo_inav_1.7.1_dump.txt]
2017-06-08 Purged old configuration files
    [sp3evo_inav_1.6.1_defaults.txt, sp3evo_inav_1.6.1_dump.txt, sp3evo_inav_1.7_defaults.txt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]
2017-06-08 Upgraded GPS provider to UBLOX7
    [sp3evo_inav_1.7.1_dump.txt]
2017-08-20 changed nav control mode to CRUISE, increased nav speed to 5 m/s
    [sp3evo_inav_1.7.1_dump.txt]
2017-08-24 Added configuration for inav 1.7.2
    [sp3evo_inav_1.7.2_defaults.txt, sp3evo_inav_1.7.2_dump.txt]
2018-03-01 Added configuration for inav 1.8
    [sp3evo_inav_1.8_defaults.txt, sp3evo_inav_1.8_dump.txt]
2018-03-01 changed material for landing gear and camera frame
    [camera_frame.stl, l_gear.stl]
2018-06-06 Configuration changed to ease upgrade to version 1.9+
    [sp3evo_inav_1.8_dump.txt]
2018-09-24 changed VTX to tramp HV
    [body.stl]
2018-09-30 Added support for R9slim antenna, adjusted CoG based
    [body.stl]
2018-09-30 Added leftover configuration files for old FC
    [sp3evo_inav_1.9.1_defaults.txt, sp3evo_inav_1.9.1_dump.txt, sp3evo_inav_2.0_defaults.txt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]
2018-09-30 Removed configuration files for old FC
    [sp3evo_inav_1.7.1_defaults.txt, sp3evo_inav_1.7.1_dump.txt, sp3evo_inav_1.7.2_defaults.txt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]
2018-10-01 Updated documentation
    [spracingf3_cover.stl, wiring_diagram.dwg]
2018-10-01 Explicited CAD models
2018-10-01 Re-added configuration files
    [matekF722_inav_2.0_diff.txt, matekF722_inav_2.0_dump.txt]
